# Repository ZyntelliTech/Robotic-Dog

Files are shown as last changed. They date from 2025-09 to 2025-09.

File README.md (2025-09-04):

# Robotic-Dog

## Project Description

This project aims to independently develop a high-performance robot dog capable of free movement in three-dimensional space. The robot weighs 10 kg and has an arm span of approximately 100 cm. It uses brushless servo motors to control joint motion and achieves efficient control via CAN communication.

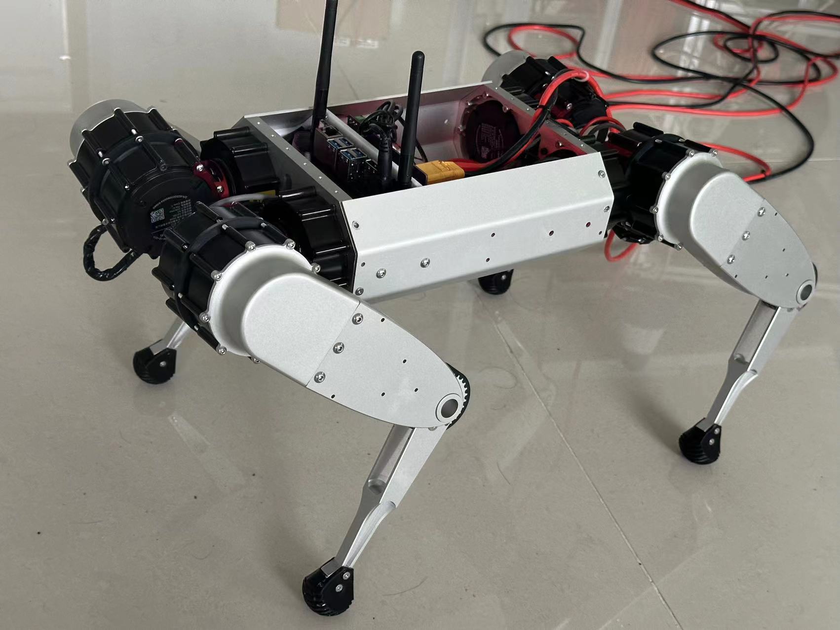
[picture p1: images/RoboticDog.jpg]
Robotic Dog


## Hardware Design
### Powertrain : 
- Each leg is equipped with three motors to ensure flexible movement in three-dimensional space. The knee joint motor is driven by a synchronous belt design to reduce energy loss during movement.
### Control system :
*  Host computer: Use NVIDIA Orin NX high-performance computer to support high-computing power applications.
* Lower computer: It consists of two STM32H7 microcontrollers, which communicate with the upper computer through SPI, parse instructions and control the motor.
* Power management: Implement three-way Buck switch step-down voltage regulator circuits of 24V-19V, 19V-5V, and 5V-3.3V, with load ripple within 30mV.
* Communication : Four CAN buses achieve a communication rate of 1Mbps, and the SPI bus supports a speed of 16Mbps, ensuring efficient and stable data transmission.

## Software Design
### Control program : 
- The host computer implements the underlying SPI sending program and gait planning program. At the same time, a Xiaomi motor driver library is developed to support control through ROS or C++.
### IoT integration : 
- Through the MQTT protocol, the robot dog's sensor data is uploaded to the IoT platform and visualized on the web to enhance the user experience.

## Mechanical Design
### Component design : 
- A total of 79 components and 276 bolt holes were designed (incomplete statistics), and the design was verified through over 100 3D printing tests to ensure its feasibility and stability.
### Material selection : 
- CNC-processed aluminum alloy parts were finally used for assembly to improve the structural strength and durability of the robot dog.

## Project Properties
### System Architecture:

- Mainly composed of upper computer, lower computer, motor and mechanical structure

- The lower computer system is composed of two STM32H7 and peripheral circuits to realize a three-level synchronous buck circuit, two SPI buses, four CAN buses, and mount 12 joint servo motors respectively.

- The lower computer and the upper computer use the SPI protocol for high-speed communication to meet the high real-time and high-frequency motion control and posture monitoring communication requirements.

- The host computer system consists of JETSON-ORIN NX and external devices to achieve posture analysis and control, laser SLAM, environment modeling, autonomous motion and navigation

### Mechanical structure:

- The mechanical structure consists of four mechanical legs, the robot body, and internal and external equipment fixing frames.

- The following is a detailed explanation of the design of the mechanical legs:

- The robotic leg consists of three joint motors and a transmission structure. The three joint motors are integrated at the hip joint through the transmission structure to reduce motion inertia.

- The overall structure is as follows:

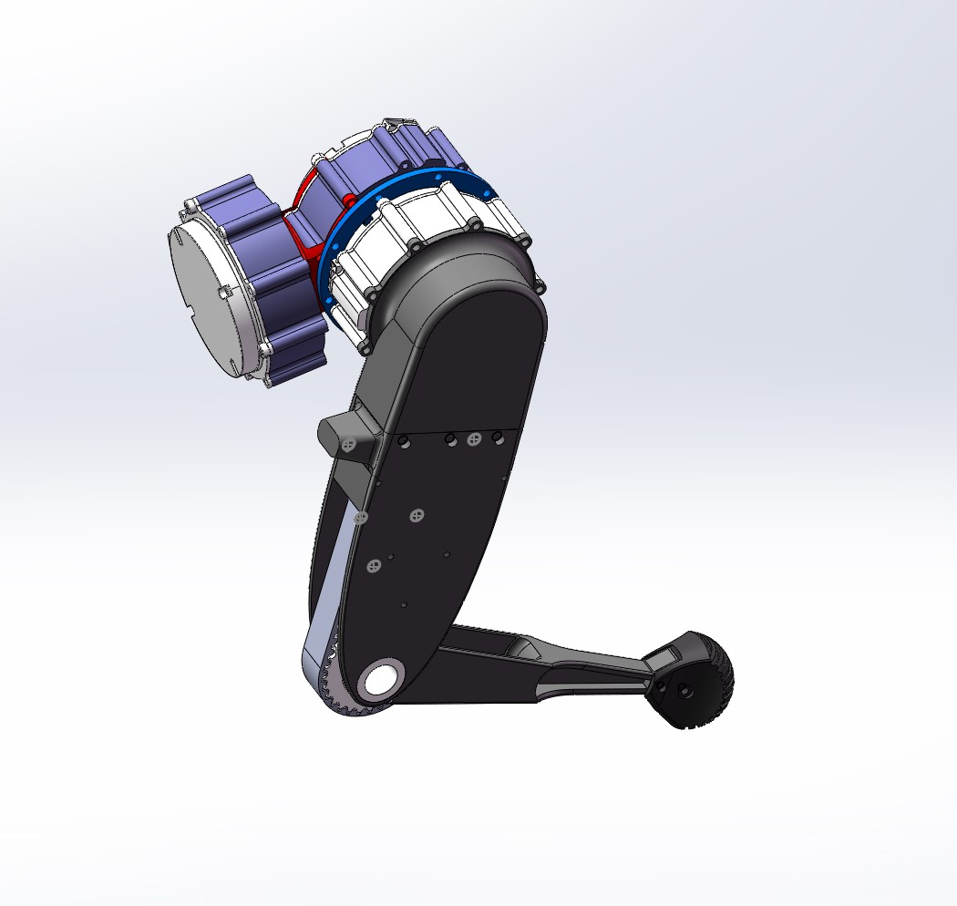
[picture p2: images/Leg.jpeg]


- Specific structural BOOM diagram (this diagram is generated for the initial version of the structure, but only some dimensions were changed later, and the overall structure remained unchanged):

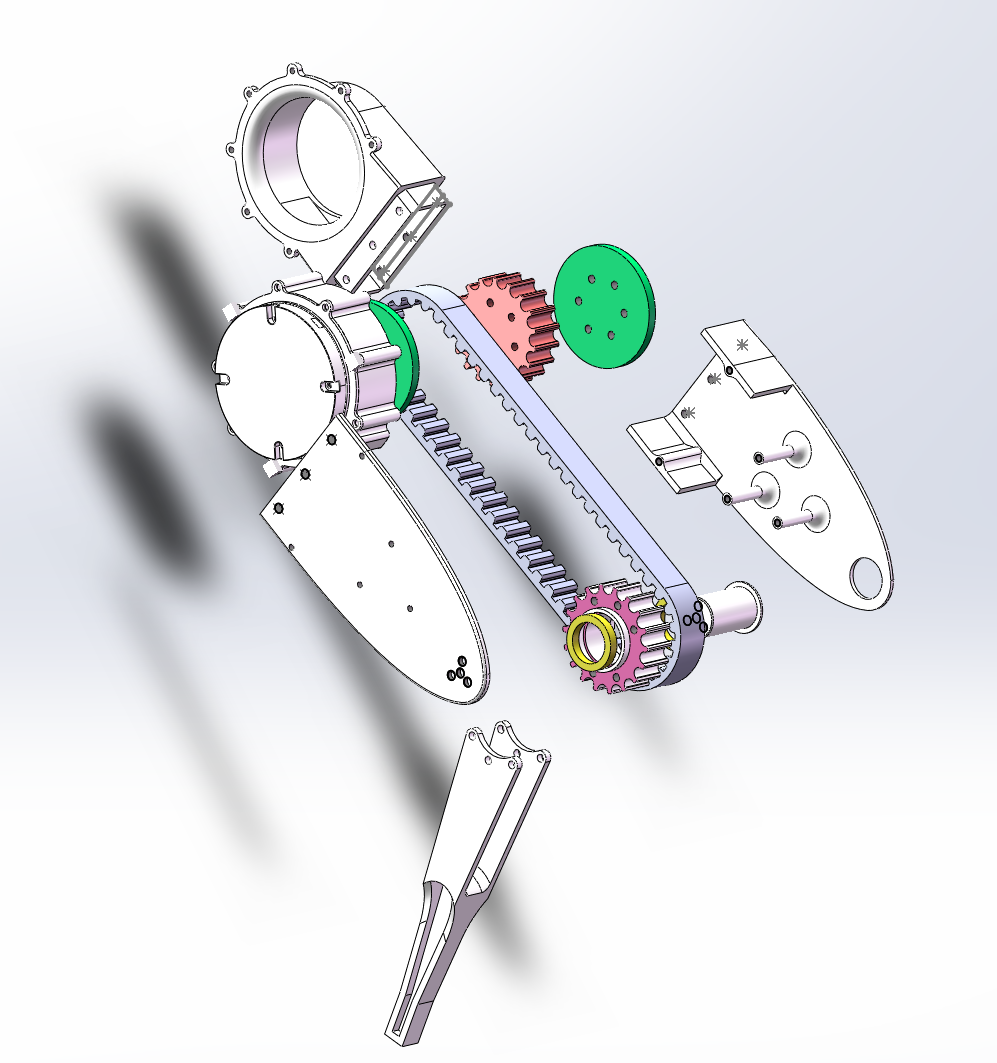
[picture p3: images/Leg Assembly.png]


- The overall structure of the robot dog:

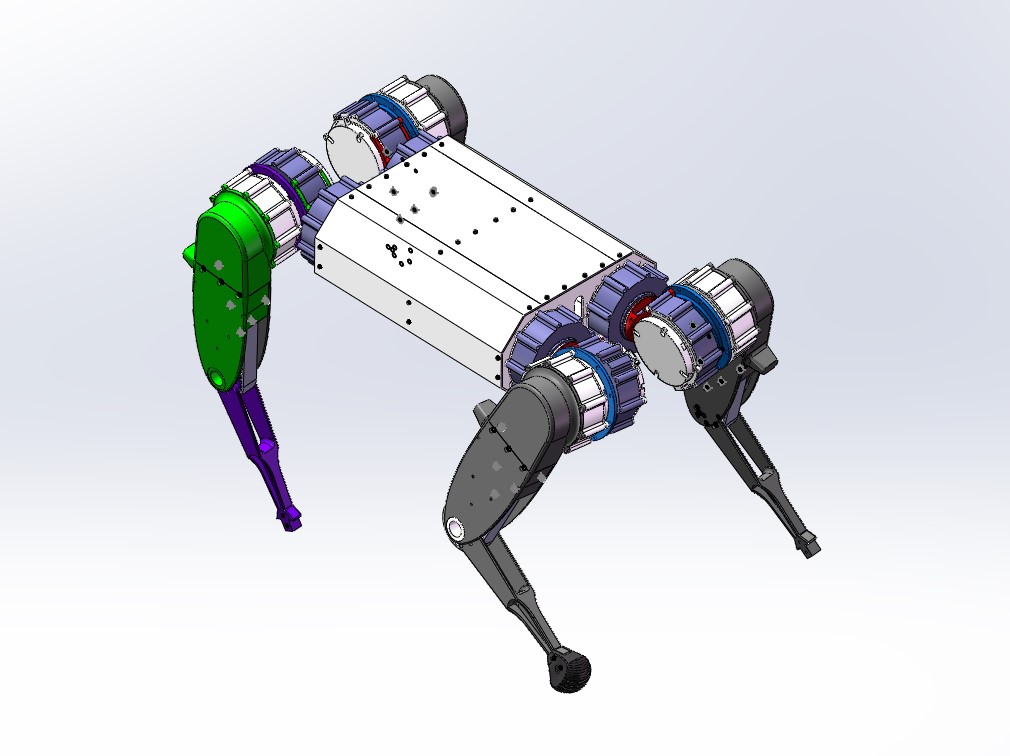
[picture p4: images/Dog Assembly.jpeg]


### Lower computer system

- Connect to the host computer via a 40PIN cable and fix it to the host computer hole position via M3 copper pillars
- The main controller is two STM32H750RCT6
- It is equipped with four CAN buses, each of which is equipped with three servo joint motors, for a total of 12 servo motors. The maximum baud rate is 1M.
- Two SPI channels, responsible for communication between each microcontroller and the host computer, with a maximum baud rate of 15M
- Onboard MPU6050 gyroscope
- Three DC-DC converters provide synchronous step-down voltages: 24V to 19V, 19V to 5V, and 5V to 3.3V. The 19V voltage powers the ORIN NX robot dog host computer (XT30), while the 5V and 3.3V voltages power the microcontroller system.
- It also integrates a power distribution board, which can provide four 24V XT60 interfaces and one 24V XT30 interface.

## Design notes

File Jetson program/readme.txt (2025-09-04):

SPI.c/h为通信程序
cybergear.c/h为我魔改后的电机驱动程序
down.c up.c为卧倒和站立程序
walk.c为对角步态程序

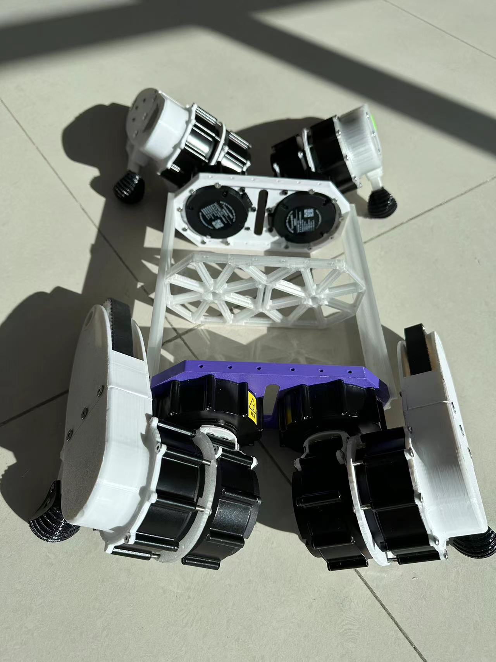
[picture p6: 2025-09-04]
images/Mechanism.jpeg

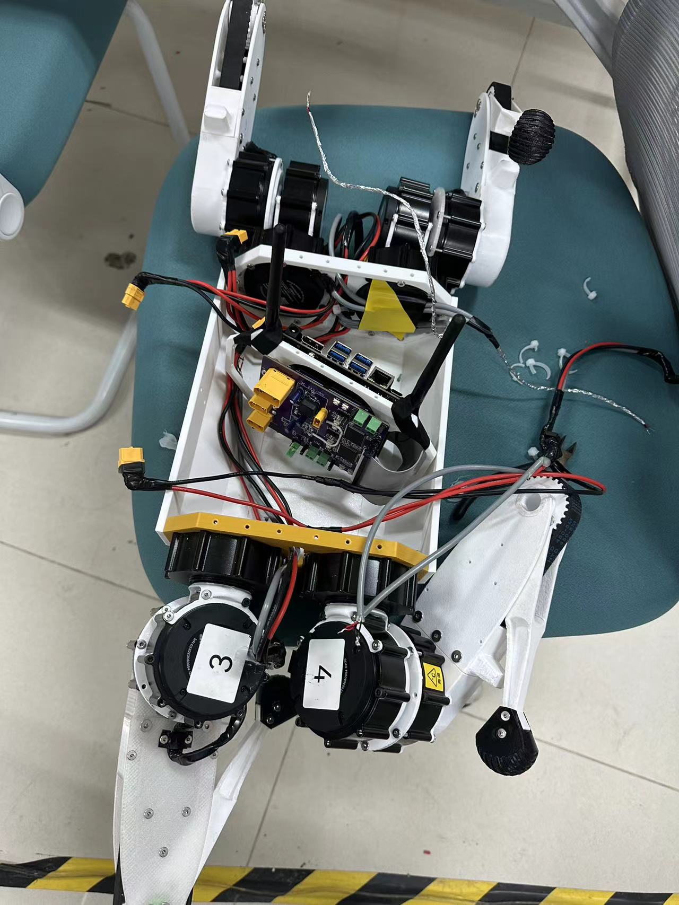
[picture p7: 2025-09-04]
images/Internal View.jpeg

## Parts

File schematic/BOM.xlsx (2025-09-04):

No. | Quantity | Comment | Designator | Footprint | Value | Manufacturer Part | Manufacturer | Supplier Part | Supplier | LCSC Stock | LCSC Price | JLCPCB Stock | JLCPCB Price
1 | 16 | 100nF | C1,C2,C3,C4,C18,C19,C20,C21,C22,C23,C24,C25,C26,C27,C48,C54 | C0603 | 100nF | CC0603KRX7R9BB104 | YAGEO(国巨) | C14663 | LCSC |  |  | 85411919 | 0.0004
2 | 8 | 10pF | C5,C6,C7,C8,C9,C10,C11,C12 | C0603 | 10pF | CL10C100JB8NNNC | SAMSUNG(三星) | C1634 | LCSC |  |  | 847311 | 0.0007
3 | 4 | 100nF | C13,C14,C43,C51 | C0603 | 100nF | CL10B104KB8NNNC | SAMSUNG(三星) | C1591 | LCSC |  |  | 7482095 | 0.0004
4 | 8 | 30pF | C15,C16,C17,C28,C31,C32,C33,C34 | C0603 | 30pF | 0603CG300J500NT | FH(风华) | C1658 | LCSC |  |  | 256265 | 0.0005
5 | 4 | 2.2uF | C29,C30,C35,C36 | C0603 | 2.2uF | CL10A225KO8NNNC | SAMSUNG(三星) | C23630 | LCSC |  |  | 1759470 | 0.0009
6 | 3 | 10uF | C37,C42,C50 | CAP-TH_BD5.0-P2.00-D0.8-FD | 10uF | ERS1HM100D11OT | AISHI(艾华集团) | C106654 | LCSC |  |  | 125026 | 0.0024
7 | 1 | 10uF | C38 | C0603 | 10uF | CL10A106KP8NNNC | SAMSUNG(三星) | C19702 | LCSC |  |  | 8751503 | 0.0008
8 | 3 | 10uF | C39,C40,C44 | C0805 | 10uF | CL21A106KOQNNNE | SAMSUNG(三星) | C1713 | LCSC |  |  | 1383031 | 0.0013
9 | 2 | 33nF | C41,C49 | C0402 | 33nF | CC0402KRX7R9BB333 | YAGEO(国巨) | C106862 | LCSC |  |  | 108402 | 0.0003
10 | 2 | 100nF | C45,C53 | C0402 | 100nF | GRM155R71H104KE14D | muRata(村田) | C77020 | LCSC |  |  | 3603048 | 0.0005
11 | 1 | 10nF | C46 | C0402 | 10nF | CC0402KRX7R7BB103 | YAGEO(国巨) | C327009 | LCSC |  |  | 271718 | 0.0002
12 | 1 | 2.2nF | C47 | C0805 | 2.2nF | CL21C222JBFNNNE | SAMSUNG(三星) | C28260 | LCSC |  |  | 113758 | 0.0045
13 | 1 | 22uF | C52 | C1206 | 22uF | CL31A226KAHNNNE | SAMSUNG(三星) | C12891 | LCSC |  |  | 1099792 | 0.0064
14 | 2 | XT30UPB-M | CN1,CN4 | CONN-TH_XT30UPB-M |  | XT30UPB-M | AMASS(艾迈斯) | C428721 | LCSC |  |  | 9927 | 0.0396
15 | 2 | XT60PW-M | CN2,CN3 | CONN-TH_XT60PW-M |  | XT60PW-M | AMASS(艾迈斯) | C98732 | LCSC |  |  | 808 | 0.0813
16 | 1 | XT90PW-M.G.Y | CN5 | CONN-TH_XT90PW-M.G.Y |  | XT90PW-M.G.Y | AMASS(艾迈斯) | C3040689 | LCSC |  |  | 4676 | 0.1179
17 | 2 | 25MHz | CRYSTAL1,CRYSTAL2 | CRYSTAL-SMD_4P-L3.2-W2.5-BL | 25MHz | CF4025M00010 | JWT(晶威特) | C5765970 | LCSC |  |  | 8711 | 0.0089
18 | 1 | B-2100S40P-B110 | H1 | HDR-TH_40P-P2.54-V-M-R2-C20-S2.54 |  | B-2100S40P-B110 | Ckmtw(灿科盟) | C124383 | LCSC |  |  | 3753 | 0.0371
19 | 5 | PZ254V-11-02P | H2,H3,H4,H5,H6 | HDR-TH_2P-P2.54-V-M |  | PZ254V-11-02P | XFCN(兴飞) | C492401 | LCSC |  |  | 889117 | 0.0019
20 | 1 | 2.54-1*3P针 | H7 | HDR-TH_3P-P2.54-V-M-1 |  | 2.54-1*3P针 | BOOMELE(博穆精密) | C49257 | LCSC |  |  | 173606 | 0.0022
21 | 2 | SBH2012S601NSP | L1,L2 | L0805 |  | SBH2012S601NSP | Sunltech(韩国顺磁) | C216152 | LCSC |  |  | 14145 | 0.0015
22 | 2 | UPZ1608E101-3R0TF | L3,L4 | L0603 |  | UPZ1608E101-3R0TF | Sunlord(顺络) | C96995 | LCSC |  |  | 70627 | 0.0013
23 | 1 | 2.7uH | L5 | IND-SMD_L4.0-W4.0_FNR40XXS | 2.7uH | FNR4012S2R7NT | cjiang(长江微电) | C167777 | LCSC |  |  | 0 | 0.0076
24 | 1 | 12uH | L6 | IND-SMD_L12.0-W12.0 | 12uH | PSPHAQ127-120M | PROD(谱罗德) | C2983062 | LCSC |  |  | 1146 | 0.0337
25 | 7 | NCD0805R1 | LED1,LED2,LED3,LED4,LED5,LED6,LED7 | LED0805-R-RD |  | NCD0805R1 | 国星光电 | C84256 | LCSC |  |  | 5982827 | 0.0019
26 | 2 | 5.1kΩ | R1,R2 | R0603 | 5.1kΩ | 0603WAF5101T5E | UNI-ROYAL(厚声) | C23186 | LCSC |  |  | 4968124 | 0.0002
27 | 4 | 10kΩ | R3,R4,R16,R21 | R0603 | 10kΩ | 0603WAF1002T5E | UNI-ROYAL(厚声) | C25804 | LCSC |  |  | 31722153 | 0.0002
28 | 4 | 120Ω | R5,R6,R7,R8 | R0603 | 120Ω | 0603WAF1200T5E | UNI-ROYAL(厚声) | C22787 | LCSC |  |  | 942284 | 0.0002
29 | 1 | 100kΩ | R9 | R0603 | 100kΩ | 0603WAF1003T5E | UNI-ROYAL(厚声) | C25803 | LCSC |  |  | 8896153 | 0.0002
30 | 7 | 1kΩ | R10,R11,R13,R14,R15,R17,R22 | R0603 | 1kΩ | 0603WAF1001T5E | UNI-ROYAL(厚声) | C21190 | LCSC |  |  | 21039229 | 0.0002
31 | 1 | 309kΩ | R12 | R0402 | 309kΩ | RC-02W3093FT | FH(风华) | C321438 | LCSC |  |  | 4476 | 0.0001
32 | 1 | 52.3kΩ | R18 | R0603 | 52.3kΩ | 0603WAF5232T5E | UNI-ROYAL(厚声) | C23198 | LCSC |  |  | 163966 | 0.0002
33 | 2 | 4.7kΩ | R19,R20 | R0603 | 4.7kΩ | 0603WAF4701T5E | UNI-ROYAL(厚声) | C23162 | LCSC |  |  | 11289134 | 0.0002
34 | 1 | 226kΩ | R23 | R0402 | 226kΩ | 0402WGF2263TCE | UNI-ROYAL(厚声) | C26999 | LCSC |  |  | 6417 | 0.0001
35 | 8 | TS-1145A-B-A | SW1,SW2,SW3,SW4,SW5,SW6,SW7,SW8 | SW-SMD_4P-L4.2-W3.2-P2.15-LS5.2 |  | TS-1145A-B-A | XKB Connectivity(中国星坤) | C318904 | LCSC |  |  | 10849 | 0.0069
36 | 4 | M3螺丝 | TP1,TP2,TP3,TP4 | M3螺丝 |  |  |  |  |  | 551 | 5.6361
37 | 2 | STM32H750VBT6 | U1,U2 | LQFP-100_L14.0-W14.0-P0.50-LS16.0-BL |  | STM32H750VBT6 | ST(意法半导体) | C404010 | LCSC |  |  | 882 | 0.5904
38 | 4 | TJA1051T/3/1J | U3,U4,U7,U8 | SOIC-8_L4.9-W3.9-P1.27-LS6.0-BL |  | TJA1051T/3/1J | NXP(恩智浦) | C38695 | LCSC |  |  | 43207 | 0.0697
39 | 4 | DB301V-3.5-2P-GN-S | U5,U6,U9,U10 | CONN-TH_DB301V-3.5-2P-GN |  | DB301V-3.5-2P-GN-S | DORABO(地博电气) | C695629 | LCSC |  |  | 62390 | 0.0134
40 | 2 | GPHA101-0402A001A1BA | U11,U12 | HDR-TH_4P-P2.54-V-M |  | GPHA101-0402A001A1BA | GREENCONN(格康) | C7434478 | LCSC |  |  | 0 | 0.0102
41 | 1 | TPS82130SILR | U13 | USIP-8_L3.0-W2.8-P0.65-TL-EP |  | TPS82130SILR | TI(德州仪器) | C473914 | LCSC |  |  | 7105 | 0.1593
42 | 1 | MPU-6050 | U14 | QFN-24_L4.0-W4.0-P0.50-BL-EP2.7 |  | MPU-6050 | TDK InvenSense(应美盛) | C24112 | LCSC |  |  | 24289 | 0.9579
43 | 2 | TPS62933DRLR | U15,U18 | SOT-583-8_L2.1-W1.2-P0.50-LS1.6-BR |  | TPS62933DRLR | TI(德州仪器) | C3200405 | LCSC |  |  | 16461 | 0.0534
44 | 2 | XT60 | U16,U17 | CONN-TH_XT60 |  | XT60 | AMASS(艾迈斯) | C98733 | LCSC |  |  | 355 | 0.0502
45 | 2 | 32.768kHz | X1,X2 | FC-135R_L3.2-W1.5 | 32.768kHz | Q13FC13500004 | EPSON(爱普生) | C32346 | LCSC |  |  | 714276 | 0.0254

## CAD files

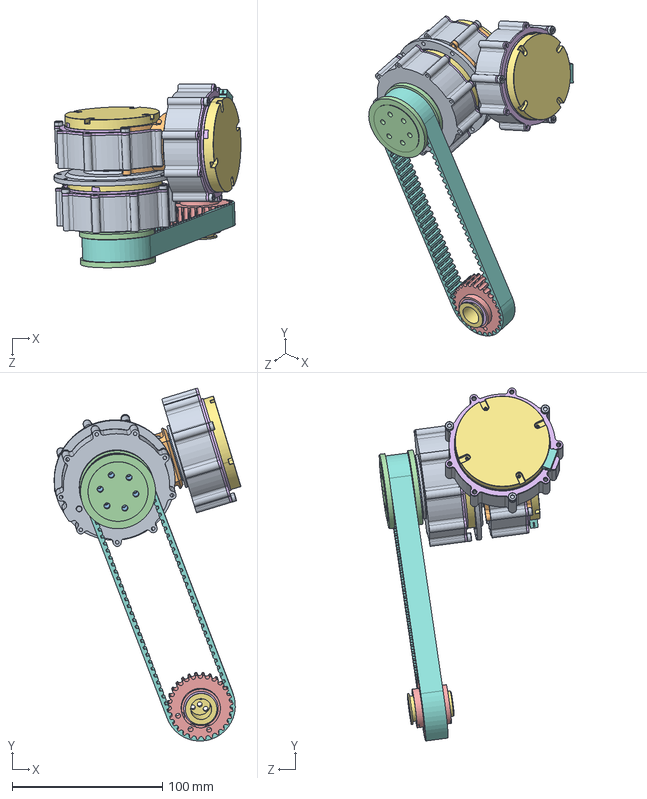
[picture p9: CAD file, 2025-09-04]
Mechanical components/Left Leg Assembly.SLDASM
124.5 x 235.1 x 122.3 mm
1_1_06_EB673-504_1_1_1_1_1.stp x 3
1_2_04_670601_1_1_1_1_1.stp x 3
1_1_02_EB671-500_1_1_1_1_1.stp x 3
1_2_04_694000_1_1_1_1_1.stp x 3
1_2_06_000213_1_1_1_1_1.stp x 3
1_1_31_QT-642_1_1_1_1_1.stp x 3
1_1_06_EB673-502_1_1_1_1_1.stp x 3
DUANZI_1_3_1_1_1_1_1_1.stp x 3
LUODING_1_1.stp x 9
0411-2_4_1_3_1.stp x 3
带轮
带轮挡边 x 2
膝关节带轮
轴承 x 2
膝关节转轴
5m同步带1
连接盘
肩关节连接器

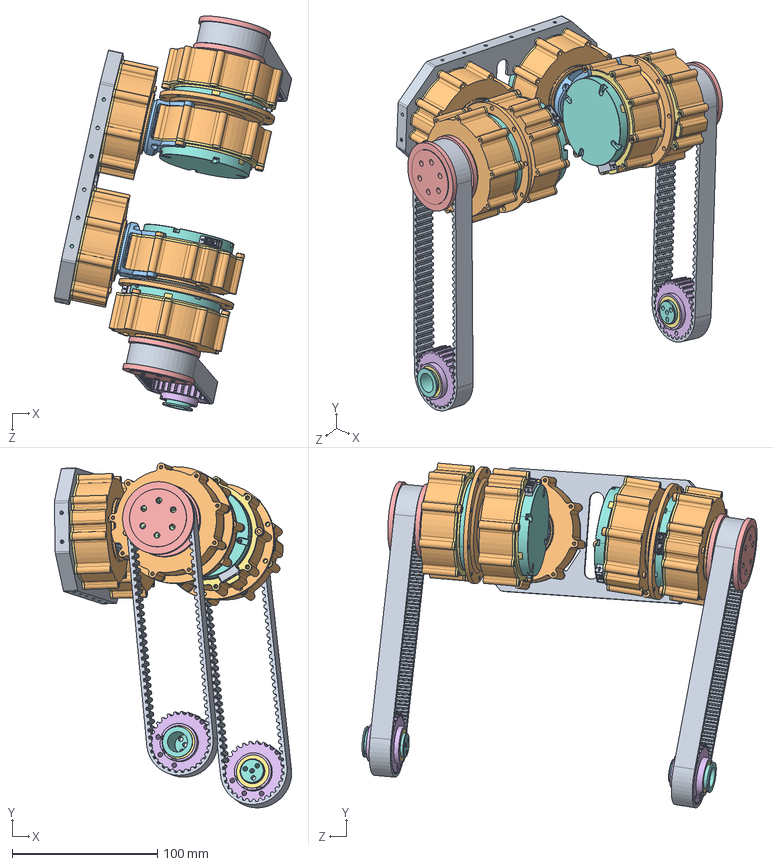
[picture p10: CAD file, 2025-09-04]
Mechanical components/Hin Legs.SLDASM
163.2 x 237.2 x 271.7 mm
肩膀
1_1_06_EB673-504_1_1_1_1_1.stp x 6
1_2_04_670601_1_1_1_1_1.stp x 6
1_1_02_EB671-500_1_1_1_1_1.stp x 6
1_2_04_694000_1_1_1_1_1.stp x 6
1_2_06_000213_1_1_1_1_1.stp x 6
1_1_31_QT-642_1_1_1_1_1.stp x 6
1_1_06_EB673-502_1_1_1_1_1.stp x 6
DUANZI_1_3_1_1_1_1_1_1.stp x 6
LUODING_1_1.stp x 18
0411-2_4_1_3_1.stp x 6
带轮 x 2
带轮挡边 x 4
膝关节带轮 x 2
轴承 x 4
膝关节转轴 x 2
5m同步带1 x 2
连接盘 x 2
肩关节连接器 x 2

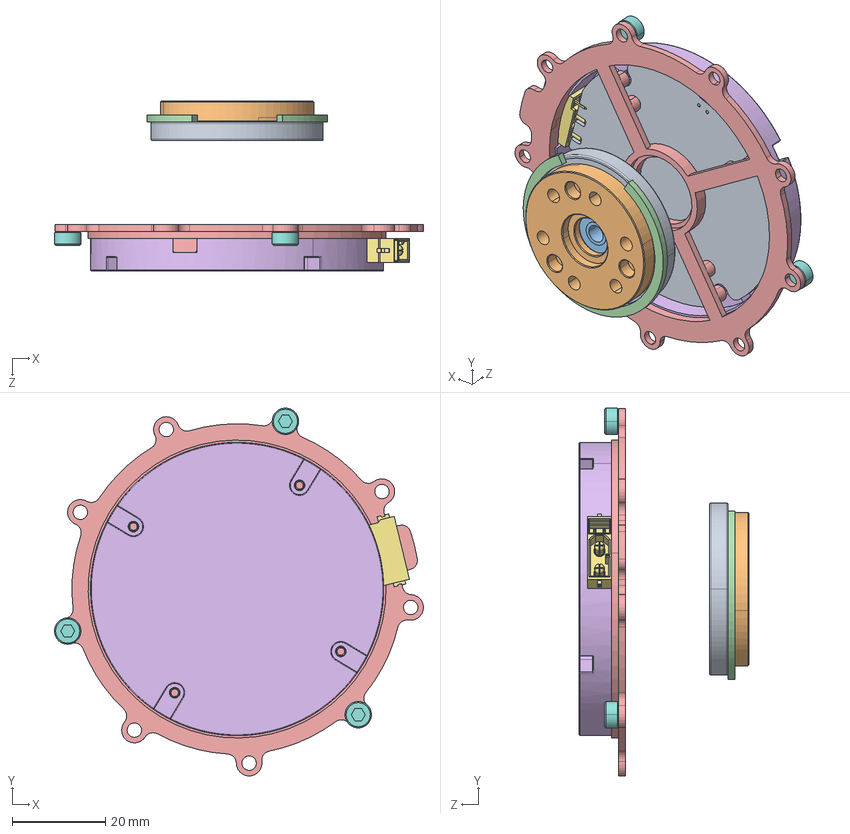
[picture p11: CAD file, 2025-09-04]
Mechanical components/CyberGearmotor.stp.SLDASM
79.3 x 79.0 x 36.5 mm
1_2_04_670601_1_1_1_1_1.stp
1_1_02_EB671-500_1_1_1_1_1.stp
1_2_04_694000_1_1_1_1_1.stp
1_2_06_000213_1_1_1_1_1.stp
1_1_31_QT-642_1_1_1_1_1.stp
1_1_06_EB673-502_1_1_1_1_1.stp
DUANZI_1_3_1_1_1_1_1_1.stp
LUODING_1_1.stp x 3
0411-2_4_1_3_1.stp

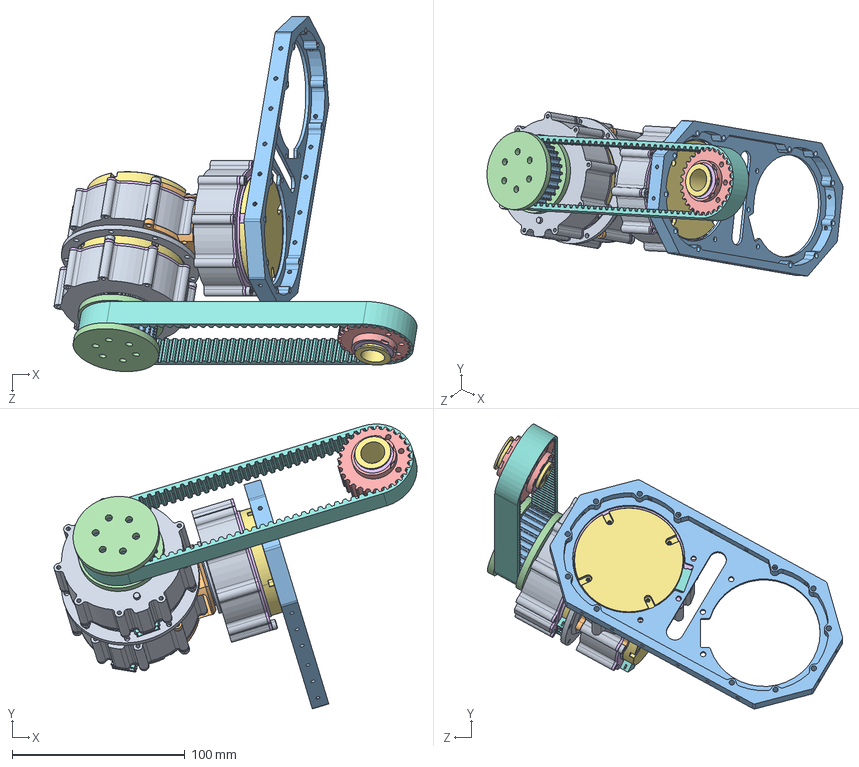
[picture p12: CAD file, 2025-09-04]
Mechanical components/Testing robotic leg assembly.SLDASM
210.0 x 164.8 x 205.5 mm
1_1_06_EB673-504_1_1_1_1_1.stp x 3
1_2_04_670601_1_1_1_1_1.stp x 3
1_1_02_EB671-500_1_1_1_1_1.stp x 3
1_2_04_694000_1_1_1_1_1.stp x 3
1_2_06_000213_1_1_1_1_1.stp x 3
1_1_31_QT-642_1_1_1_1_1.stp x 3
1_1_06_EB673-502_1_1_1_1_1.stp x 3
DUANZI_1_3_1_1_1_1_1_1.stp x 3
LUODING_1_1.stp x 9
0411-2_4_1_3_1.stp x 3
带轮
带轮挡边 x 2
膝关节带轮
轴承 x 2
膝关节转轴
5m同步带1
连接盘
肩关节连接器
肩膀

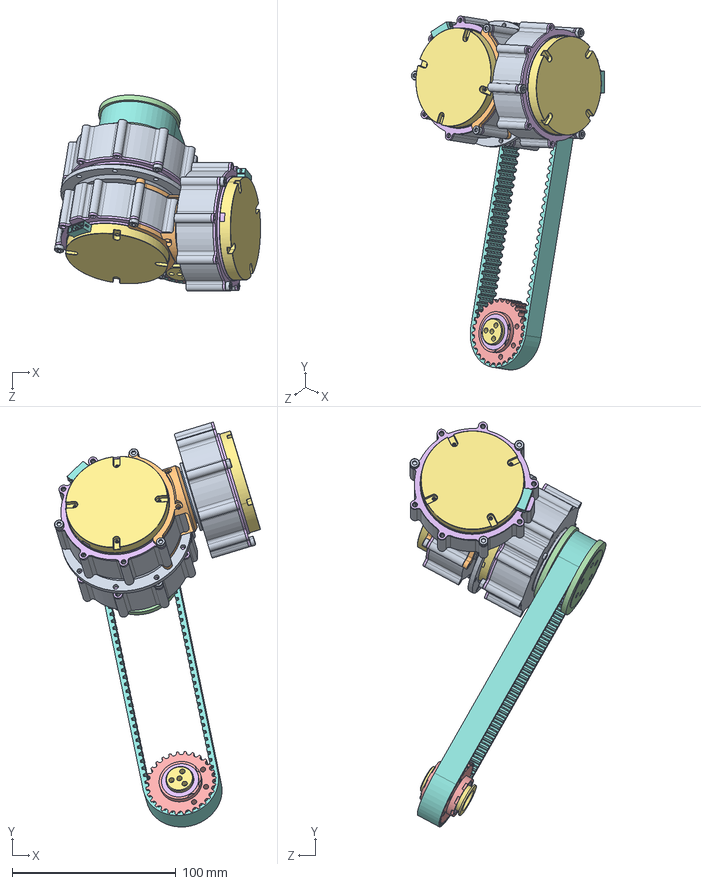
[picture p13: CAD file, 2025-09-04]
Mechanical components/Right Rear Leg Assembly.SLDASM
125.9 x 247.4 x 119.6 mm
1_1_06_EB673-504_1_1_1_1_1.stp x 3
1_2_04_670601_1_1_1_1_1.stp x 3
1_1_02_EB671-500_1_1_1_1_1.stp x 3
1_2_04_694000_1_1_1_1_1.stp x 3
1_2_06_000213_1_1_1_1_1.stp x 3
1_1_31_QT-642_1_1_1_1_1.stp x 3
1_1_06_EB673-502_1_1_1_1_1.stp x 3
DUANZI_1_3_1_1_1_1_1_1.stp x 3
LUODING_1_1.stp x 9
0411-2_4_1_3_1.stp x 3
带轮
带轮挡边 x 2
膝关节带轮
轴承 x 2
膝关节转轴
5m同步带1
连接盘
肩关节连接器

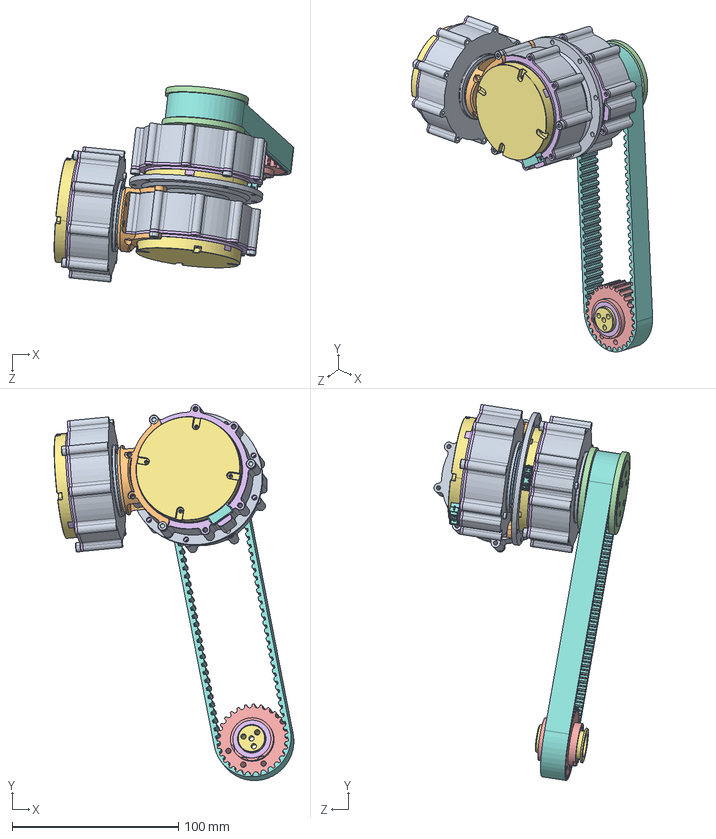
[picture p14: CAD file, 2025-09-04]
Mechanical components/Left Rear Leg Assembly.SLDASM
144.1 x 226.1 x 117.9 mm
1_1_06_EB673-504_1_1_1_1_1.stp x 3
1_2_04_670601_1_1_1_1_1.stp x 3
1_1_02_EB671-500_1_1_1_1_1.stp x 3
1_2_04_694000_1_1_1_1_1.stp x 3
1_2_06_000213_1_1_1_1_1.stp x 3
1_1_31_QT-642_1_1_1_1_1.stp x 3
1_1_06_EB673-502_1_1_1_1_1.stp x 3
DUANZI_1_3_1_1_1_1_1_1.stp x 3
LUODING_1_1.stp x 9
0411-2_4_1_3_1.stp x 3
带轮
带轮挡边 x 2
膝关节带轮
轴承 x 2
膝关节转轴
5m同步带1
连接盘
肩关节连接器

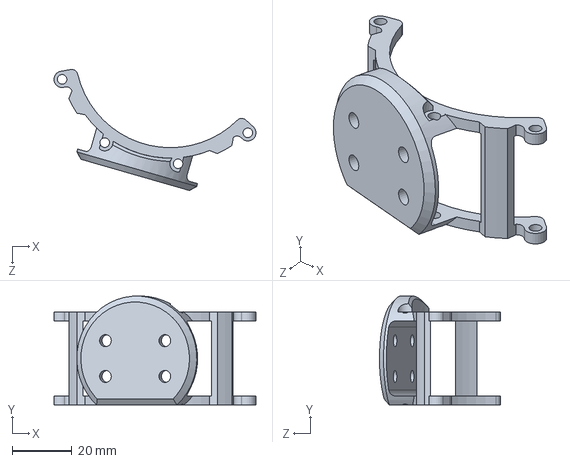
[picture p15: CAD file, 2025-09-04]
Mechanical components/Shoulder Joint Connector.SLDPRT
67.9 x 36.6 x 40.7 mm

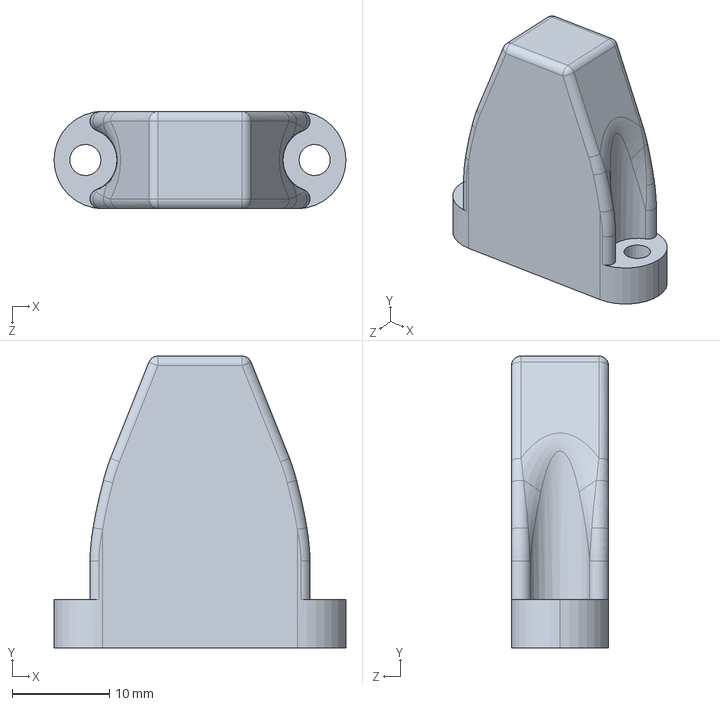
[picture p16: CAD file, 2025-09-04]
Mechanical components/High Cushion.SLDPRT
30.0 x 30.0 x 10.0 mm

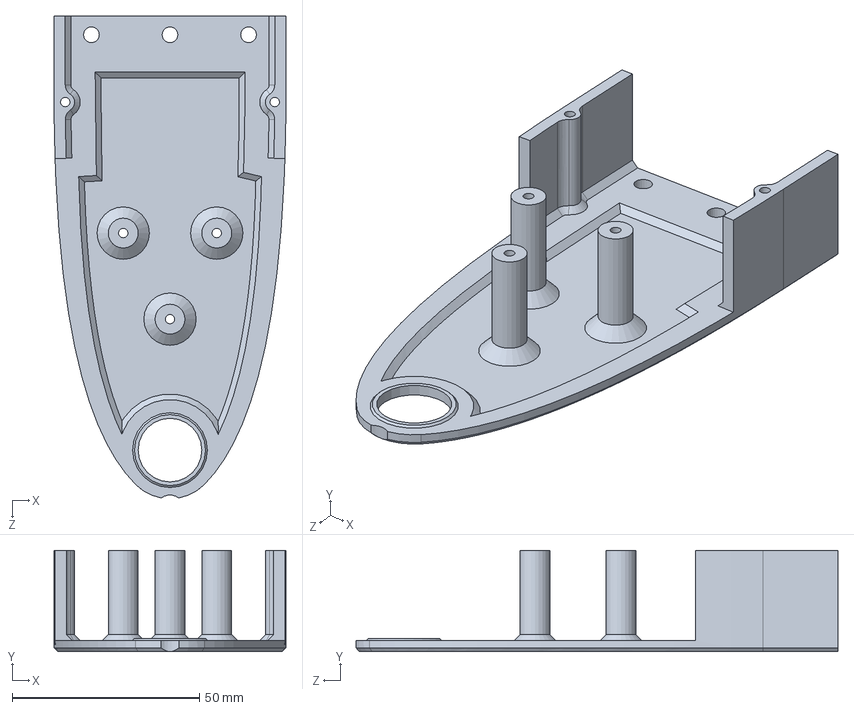
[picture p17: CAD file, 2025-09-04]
Mechanical components/Thigh Front.SLDPRT
62.0 x 27.0 x 128.8 mm

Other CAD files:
Mechanical components/0714_ASM_1_ASM_1_ASM_1_ASM.stp.SLDASM
Mechanical components/3_1_02_067_0003_ASM_ASM_1_ASM_1_ASM.stp.SLDASM
Mechanical components/0518_ASM_2_ASM_1_ASM_1_ASM_1_AS_ASM.stp.SLDASM
Mechanical components/3_1_02_067_0003_ASM_1_ASM_1_ASM_ASM.stp.SLDASM
Mechanical components/ASM0002_ASM_1_ASM.stp.SLDASM
Mechanical components/ASM0002_ASM_1_ASM_1_ASM.stp.SLDASM
Mechanical components/1_1_06_EB673-504_1_1_1_1_1.stp.SLDPRT
Mechanical components/0411-2_4_1_3_1.stp.SLDPRT
Mechanical components/1_2_06_000213_1_1_1_1_1.stp.SLDPRT
Mechanical components/12345_ASM_1_ASM_2_ASM_1_ASM_1_A_ASM.stp.SLDASM
Mechanical components/1_1_02_EB671-500_1_1_1_1_1.stp.SLDPRT
Mechanical components/1_1_06_EB673-502_1_1_1_1_1.stp.SLDPRT
Mechanical components/1_1_31_QT-642_1_1_1_1_1.stp.SLDPRT
Mechanical components/1_2_04_670601_1_1_1_1_1.stp.SLDPRT
Mechanical components/1_2_04_694000_1_1_1_1_1.stp.SLDPRT
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

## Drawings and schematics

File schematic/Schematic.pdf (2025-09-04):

VDD 50 | PB12 51 PB13 52 PB14 53 PB15 54 PD8 55 PD9 56 PD10 57 PD11 58 PD12 59 PD13 60 PD14 61 PD15 62 PC6 63 PC7 64 PC8 65 PC9 66 PA8 67 PA9 68 PA10 69 PA11 70 PA12 71 PA13 72 VCAP 73 VSS 74 VDD 75 PA14 76 PA15 77 PC10 78 PC11 79 PC12 80 PD0 81 PD1 82 PD2 83 PD3 84 PD4 85 PD5 86 PD6 87 PD7 88 PB3 89 PB4 90 PB5 91 PB6 92 PB7 93 BOOT0 94 PB8 95 PB9 96 PE0 97 PE1 98 VSS 99 VDD 100
BOOT | VCC

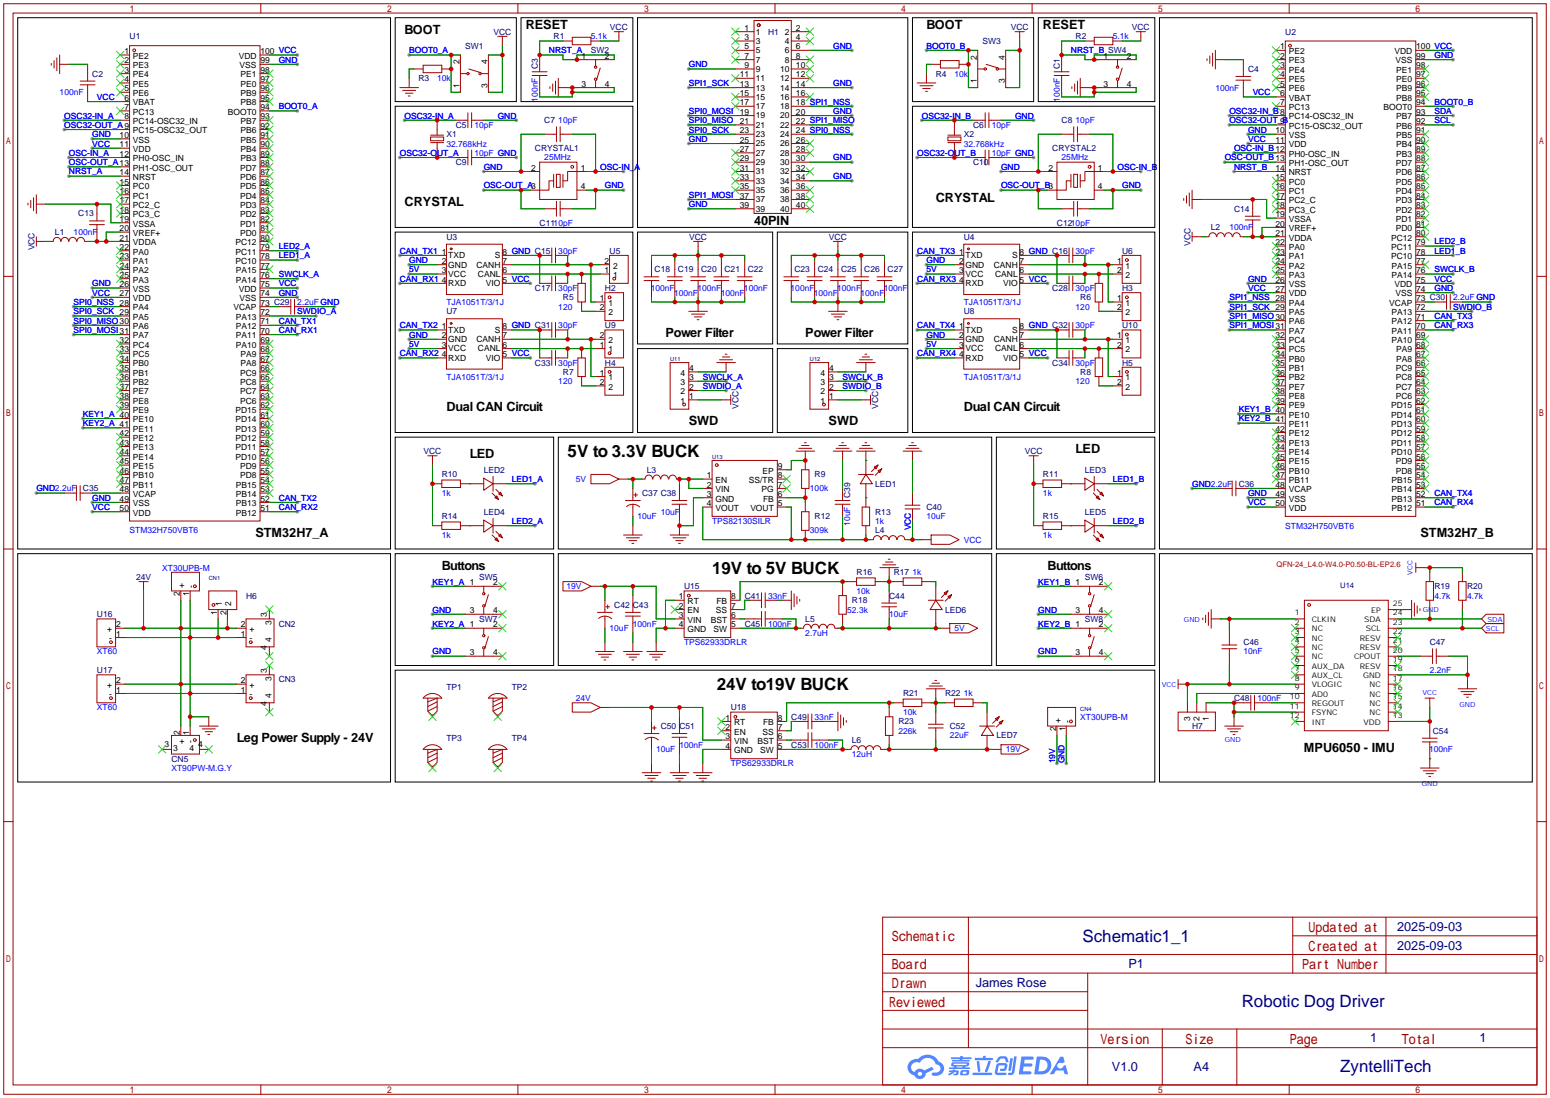
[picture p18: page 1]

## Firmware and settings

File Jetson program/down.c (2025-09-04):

#include "main.h"
#include "cybergear.h"
#include "stdio.h"
#include <stdint.h>
#include "SPI.h"
#include <unistd.h>


#define spd 3
#define spd1 0.5
void delay_ms(unsigned int milliseconds) {
    usleep(milliseconds * 1000);  // 将毫秒转换为微秒
}
int main()
{
    SPI_inti();
    MI_Motor mi_motor[12];
    /* code */
    init_cybergear(&mi_motor[0], 0X11, 1);
     delay_ms(1);
    init_cybergear(&mi_motor[1], 0X12, 1);
     delay_ms(1);
    init_cybergear(&mi_motor[2], 0X13, 1);
     delay_ms(1);
    init_cybergear(&mi_motor[3], 0X21, 1);
     delay_ms(1);
    init_cybergear(&mi_motor[4], 0X22, 1);
     delay_ms(1);
    init_cybergear(&mi_motor[5], 0X23, 1);
    delay_ms(1);
    init_cybergear(&mi_motor[5], 0X23, 1);
    delay_ms(1);
    init_cybergear(&mi_motor[5], 0X23, 1);
     delay_ms(1);
    init_cybergear(&mi_motor[6], 0X31, 1);
     delay_ms(1);
    init_cybergear(&mi_motor[7], 0X32, 1);
     delay_ms(1);
    init_cybergear(&mi_motor[8], 0X33, 1);
     delay_ms(1);
    init_cybergear(&mi_motor[9], 0X41, 1);
     delay_ms(1);
    init_cybergear(&mi_motor[10], 0X42, 1);
     delay_ms(1);
    init_cybergear(&mi_motor[11], 0X43, 1);
     delay_ms(1);
    //for(int i=0;i<=11;i++) set_zeropos_cybergear(&mi_motor[i]);
    //for(int i=0;i<=11;i++) Set_Motor_Parameter(&mi_motor[i],loc_kp,40,'f');
    //for(int i=0;i<=11;i++) start_cybergear(&mi_motor[i]); 
    
  Set_Motor_Parameter(&mi_motor[0],Limit_Spd ,spd,'f');
    delay_ms(1);
    Set_Motor_Parameter(&mi_motor[0],Loc_Ref ,0,'f');
    delay_ms(1);
    Set_Motor_Parameter(&mi_motor[3],Limit_Spd ,spd,'f');
    delay_ms(1);
    Set_Motor_Parameter(&mi_motor[3],Loc_Ref ,0,'f');
    delay_ms(1);
    Set_Motor_Parameter(&mi_motor[6],Limit_Spd ,spd,'f');
    delay_ms(1);
    Set_Motor_Parameter(&mi_motor[6],Loc_Ref ,0,'f');
    delay_ms(1);
    Set_Motor_Parameter(&mi_motor[9],Limit_Spd ,spd,'f');
    delay_ms(1);
    Set_Motor_Parameter(&mi_motor[9],Loc_Ref ,0,'f');
    
    
    //delay_ms(1000);
    
    Set_Motor_Parameter(&mi_motor[1],Limit_Spd ,spd,'f');
    delay_ms(1);
    Set_Motor_Parameter(&mi_motor[1],Loc_Ref ,0,'f');
    delay_ms(1);
    Set_Motor_Parameter(&mi_motor[4],Limit_Spd ,spd,'f');
    delay_ms(1);
    Set_Motor_Parameter(&mi_motor[4],Loc_Ref ,0,'f');
    delay_ms(1);
    Set_Motor_Parameter(&mi_motor[7],Limit_Spd ,spd,'f');
    delay_ms(1);
    Set_Motor_Parameter(&mi_motor[7],Loc_Ref ,0,'f');
    delay_ms(1);
    Set_Motor_Parameter(&mi_motor[10],Limit_Spd ,spd,'f');
    delay_ms(1);
    Set_Motor_Parameter(&mi_motor[10],Loc_Ref ,0,'f');
    
    delay_ms(1000);

    Set_Motor_Parameter(&mi_motor[2],Limit_Spd ,spd1,'f');
    delay_ms(1);
    Set_Motor_Parameter(&mi_motor[2],Loc_Ref ,0,'f');
    delay_ms(1);
    Set_Motor_Parameter(&mi_motor[5],Limit_Spd ,spd1,'f');
    delay_ms(1);
    Set_Motor_Parameter(&mi_motor[5],Loc_Ref ,0,'f');
    delay_ms(1);
    Set_Motor_Parameter(&mi_motor[8],Limit_Spd ,spd1,'f');
    delay_ms(1);
    Set_Motor_Parameter(&mi_motor[8],Loc_Ref ,0,'f');
    delay_ms(1);
    Set_Motor_Parameter(&mi_motor[11],Limit_Spd ,spd1,'f');
    delay_ms(1);
    Set_Motor_Parameter(&mi_motor[11],Loc_Ref ,0,'f');
    delay_ms(1);
    
    return 0;
}

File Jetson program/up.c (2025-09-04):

#include "main.h"
#include "cybergear.h"
#include "stdio.h"
#include <stdint.h>
#include "SPI.h"
#include <unistd.h>
void delay_ms(unsigned int milliseconds) {
    usleep(milliseconds * 1000);  // 将毫秒转换为微秒
}
int main()
{
    SPI_inti();
    MI_Motor mi_motor[12];
    /* code */
    init_cybergear(&mi_motor[0], 0X11, 1);
     delay_ms(1);
    init_cybergear(&mi_motor[1], 0X12, 1);
     delay_ms(1);
    init_cybergear(&mi_motor[2], 0X13, 1);
     delay_ms(1);
    init_cybergear(&mi_motor[3], 0X21, 1);
     delay_ms(1);
    init_cybergear(&mi_motor[4], 0X22, 1);
     delay_ms(1);
    init_cybergear(&mi_motor[5], 0X23, 1);
    delay_ms(1);
    init_cybergear(&mi_motor[5], 0X23, 1);
    delay_ms(1);
    init_cybergear(&mi_motor[5], 0X23, 1);
     delay_ms(1);
    init_cybergear(&mi_motor[6], 0X31, 1);
     delay_ms(1);
    init_cybergear(&mi_motor[7], 0X32, 1);
     delay_ms(1);
    init_cybergear(&mi_motor[8], 0X33, 1);
     delay_ms(1);
    init_cybergear(&mi_motor[9], 0X41, 1);
     delay_ms(1);
    init_cybergear(&mi_motor[10], 0X42, 1);
     delay_ms(1);
    init_cybergear(&mi_motor[11], 0X43, 1);
     delay_ms(1);
    for(int i=0;i<=11;i++) set_mode_cybergear(&mi_motor[i],1);
    for(int i=0;i<=11;i++) set_zeropos_cybergear(&mi_motor[i]);
    for(int i=0;i<=11;i++) Set_Motor_Parameter(&mi_motor[i],loc_kp,60,'f');
    for(int i=0;i<=11;i++) start_cybergear(&mi_motor[i]); 
    
    Set_Motor_Parameter(&mi_motor[2],Limit_Spd ,5,'f');
    delay_ms(1);
    Set_Motor_Parameter(&mi_motor[2],Loc_Ref ,-0.4,'f');
    delay_ms(1);
    Set_Motor_Parameter(&mi_motor[5],Limit_Spd ,5,'f');
    delay_ms(1);
    Set_Motor_Parameter(&mi_motor[5],Loc_Ref ,0.4,'f');
    delay_ms(1);
    Set_Motor_Parameter(&mi_motor[8],Limit_Spd ,5,'f');
    delay_ms(1);
    Set_Motor_Parameter(&mi_motor[8],Loc_Ref ,-0.4,'f');
    delay_ms(1);
    Set_Motor_Parameter(&mi_motor[11],Limit_Spd ,5,'f');
    delay_ms(1);
    Set_Motor_Parameter(&mi_motor[11],Loc_Ref ,0.4,'f');
    delay_ms(1000);
    
    Set_Motor_Parameter(&mi_motor[1],Limit_Spd ,5,'f');
    delay_ms(1);
    Set_Motor_Parameter(&mi_motor[1],Loc_Ref ,-0.2,'f');
    delay_ms(1);
    Set_Motor_Parameter(&mi_motor[4],Limit_Spd ,5,'f');
    delay_ms(1);
    Set_Motor_Parameter(&mi_motor[4],Loc_Ref ,0.2,'f');
    delay_ms(1);
    Set_Motor_Parameter(&mi_motor[7],Limit_Spd ,5,'f');
    delay_ms(1);
    Set_Motor_Parameter(&mi_motor[7],Loc_Ref ,0.2,'f');
    delay_ms(1);
    Set_Motor_Parameter(&mi_motor[10],Limit_Spd ,5,'f');
    delay_ms(1);
    Set_Motor_Parameter(&mi_motor[10],Loc_Ref ,-0.2,'f');
    delay_ms(1);
    
    Set_Motor_Parameter(&mi_motor[0],Limit_Spd ,5,'f');
    delay_ms(1);
    Set_Motor_Parameter(&mi_motor[0],Loc_Ref ,1.2,'f');
    delay_ms(1);
    Set_Motor_Parameter(&mi_motor[3],Limit_Spd ,5,'f');
    delay_ms(1);
    Set_Motor_Parameter(&mi_motor[3],Loc_Ref ,-1.2,'f');
    delay_ms(1);
    Set_Motor_Parameter(&mi_motor[6],Limit_Spd ,5,'f');
    delay_ms(1);
    Set_Motor_Parameter(&mi_motor[6],Loc_Ref ,-1.2,'f');
    delay_ms(1);
    Set_Motor_Parameter(&mi_motor[9],Limit_Spd ,5,'f');
    delay_ms(1);
    Set_Motor_Parameter(&mi_motor[9],Loc_Ref ,1.2,'f');
    delay_ms(1);

    
    return 0;
}
